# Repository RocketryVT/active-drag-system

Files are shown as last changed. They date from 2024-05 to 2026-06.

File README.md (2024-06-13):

# Active Drag System (ADS)
This is the main codebase for Rocketry at Virginia Tech's Active Drag System, also known colloquially as the ADS, for the 2023-2024 competition year. It runs primarily on a Raspberry Pi Pico, and its goal is to autonomously control the ADS' deployment during flight.

`Eigen` Library, `cmake`, and `arm-none-eabi-gcc` tooling required for successful build.

## Clone

**Note: You must initialize the git submodules prior to utilizing CMake for a proper build.**

```shell
git clone https://github.com/RocketryVT/active-drag-system.git
cd active-drag-system/
git submodule update --init --recursive
```

## Build (Linux)
```shell
cmake -B build
cmake --build build
```
In the event that your preferred IDE has trouble locating header files and/or is displaying incorrect errors, pass ```-DCMAKE_EXPORT_COMPILE_COMMANDS=true``` to the first CMake command above. Similarly, if you wish to compile the additional tools (e.g. reading flash, calibrating the IMU, etc.), pass ```-DCOMPILE_TOOLS=true``` to the first CMake command above as well.

## Build (Windows)
Enable WSL2 in windows
Install Ubuntu 22 LTS from Windows Store
```shell
sudo apt update && upgrade
sudo apt install build-essential cmake gcc-arm-none-eabi
```
Then to actually build:
```shell
cmake -B build
cmake --build build
```

## Build Alternative (Mac)
```shell
brew install arm-none-eabi-gcc
```
To check if installed correctly run:
```shell
ls /opt/homebrew/bin | grep "none"
```
you should see a list including but not limited to:
```shell
arm-none-eabi-gcc
arm-none-eabi-g++
```
Next:
```shell
cmake -B build
cmake --build build
```

Binary files should be located in build/src/*.uf2 after a successful build.

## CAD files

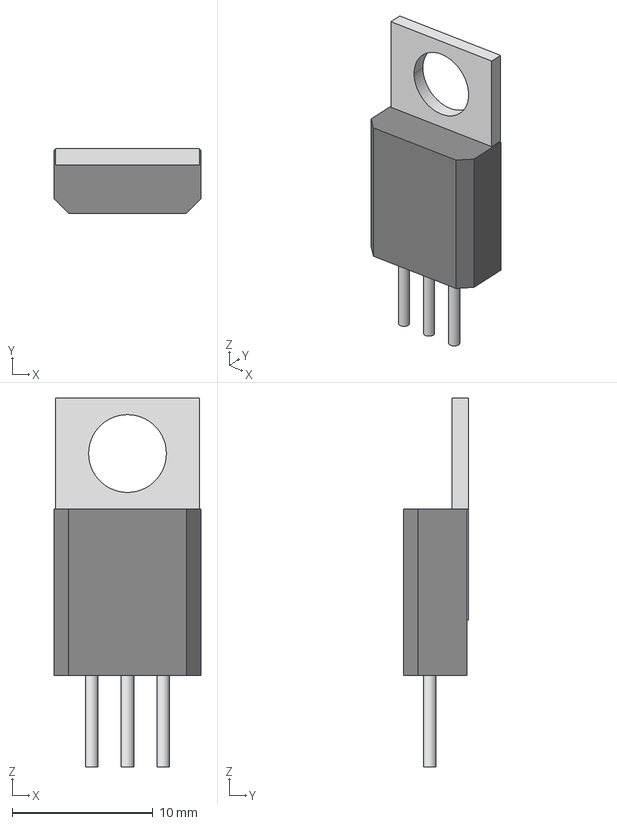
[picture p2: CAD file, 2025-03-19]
hardware/models/STP55NF06.step
10.4 x 4.60 x 26.2 mm

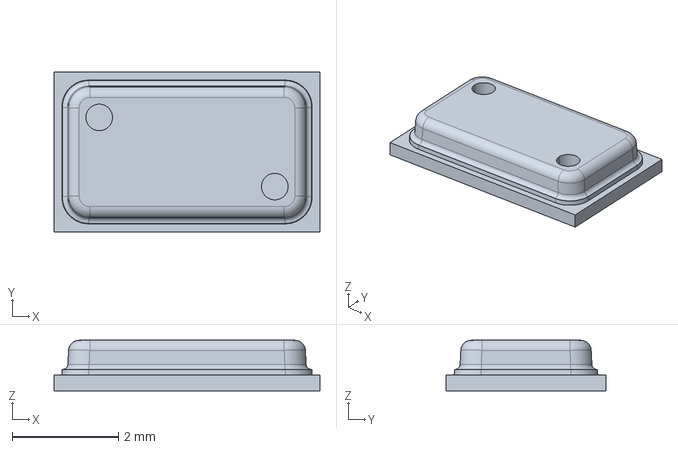
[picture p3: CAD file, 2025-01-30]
hardware/models/c-ms560702ba03-50-a-3d.stp
5.00 x 3.00 x 0.95 mm

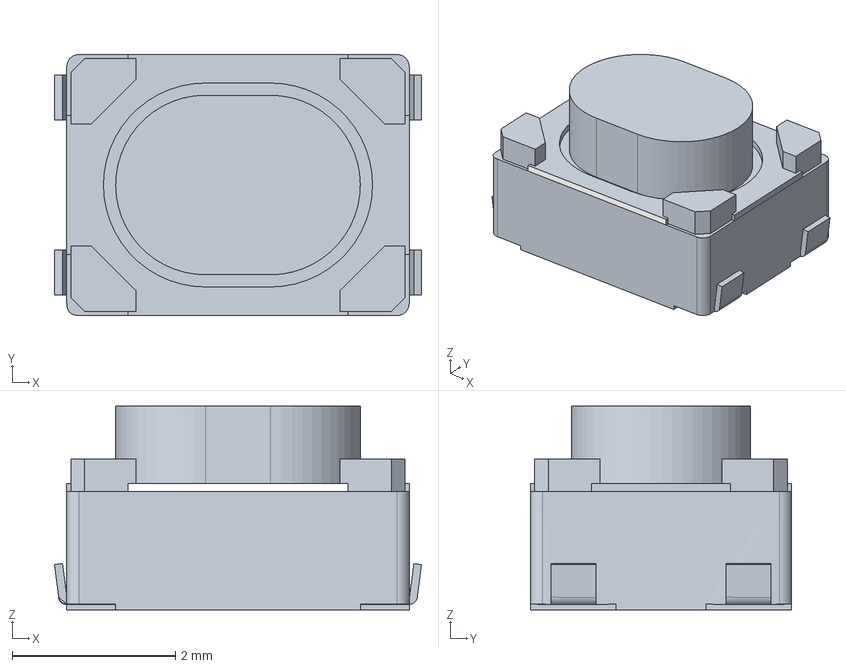
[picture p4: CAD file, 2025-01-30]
hardware/models/PTS815SJG250SMTRLFS.stp
4.50 x 3.20 x 2.50 mm
PTS815SJG250SMTRLFS_PART1
PTS815SJG250SMTRLFS_PART2
PTS815SJG250SMTRLFS_PART3

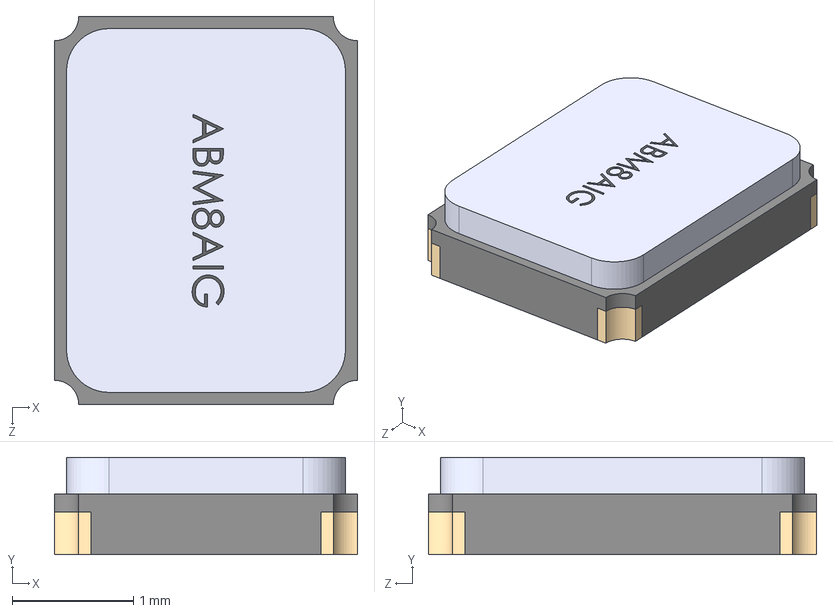
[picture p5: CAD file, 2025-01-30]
hardware/models/ABM8AIG-12.000MHZ-12-2Z-T3.step
2.50 x 0.801 x 3.20 mm

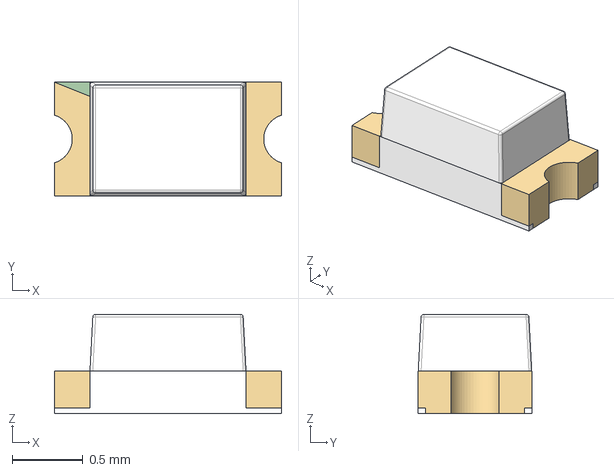
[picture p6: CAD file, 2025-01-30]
hardware/models/WL-SMCW_0603.step
1.60 x 0.8 x 0.7 mm

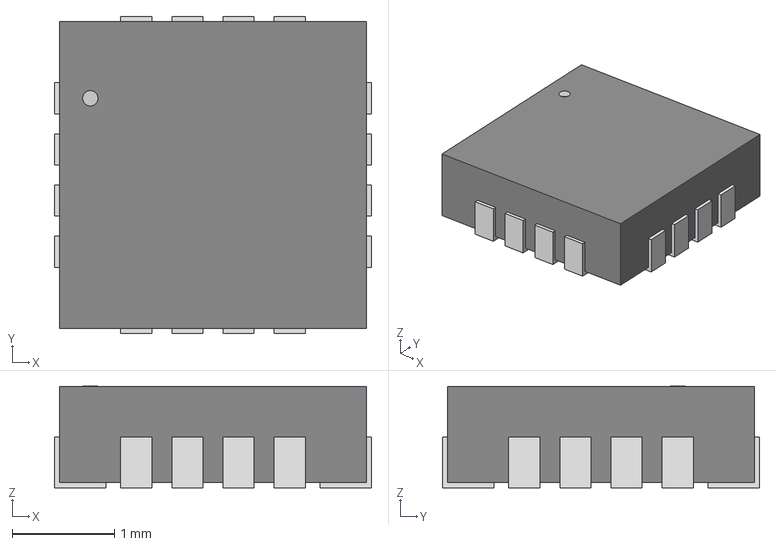
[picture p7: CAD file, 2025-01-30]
hardware/models/MMC5983MA_MEM.step
3.10 x 3.10 x 0.993 mm

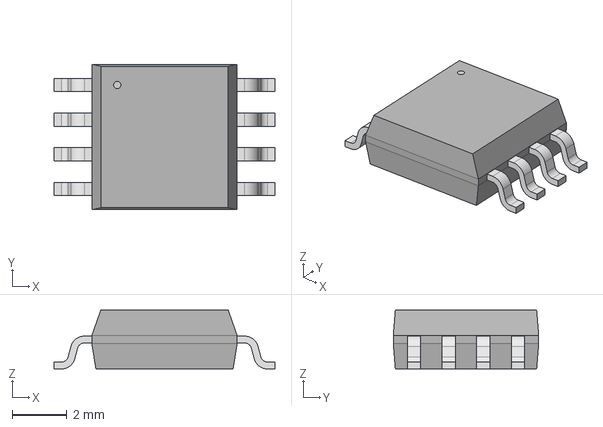
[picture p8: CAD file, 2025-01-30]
hardware/models/SOIC_128JVSIQ_WIN.step
8.10 x 5.33 x 2.16 mm

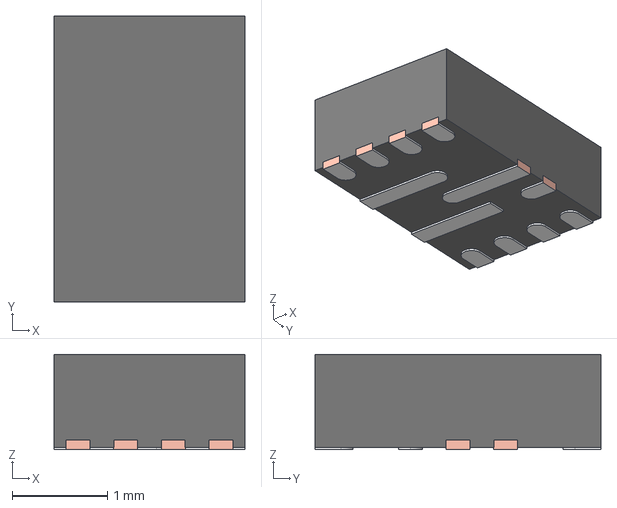
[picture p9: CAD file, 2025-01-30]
hardware/models/RJN0012A.stp
2.00 x 3.00 x 1.00 mm
FRAME
MOLD

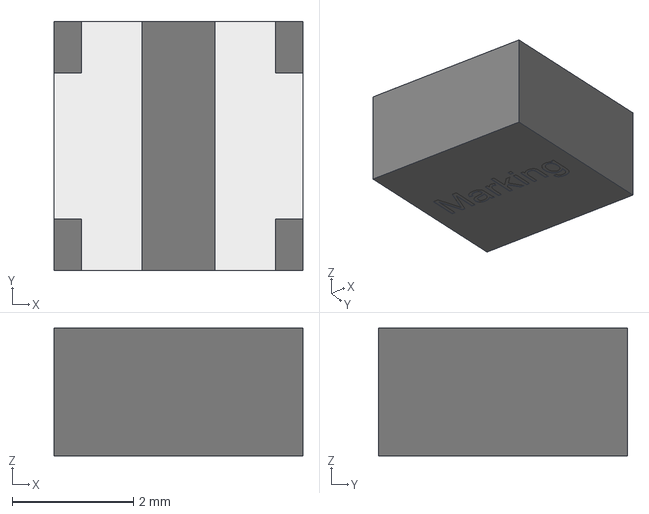
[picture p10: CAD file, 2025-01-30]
hardware/models/WE-MAIA_4020.step
4.10 x 4.10 x 2.10 mm
body_SSMC_403020
land_pattern_SSMC_403020 x 2

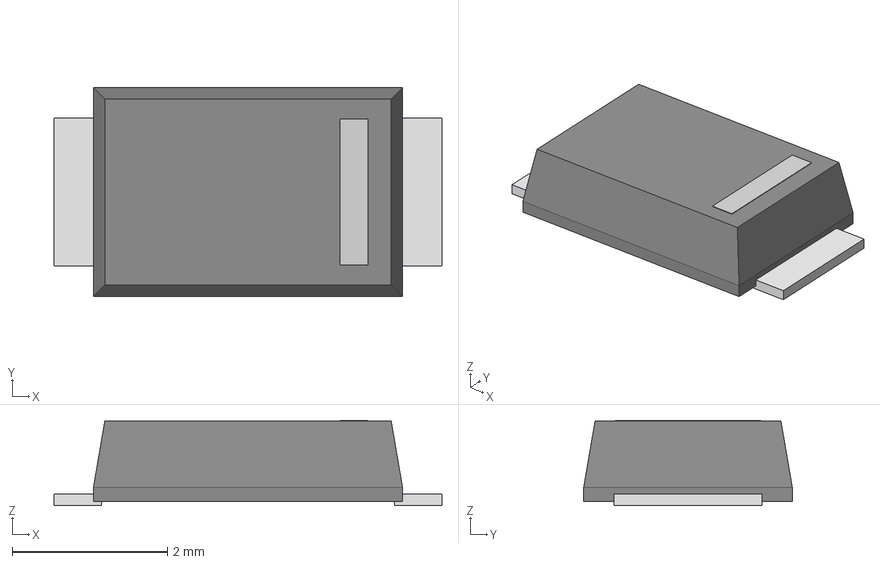
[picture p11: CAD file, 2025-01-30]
hardware/models/SDO_CFP5_SOD128_NEX.step
5.00 x 2.69 x 1.10 mm

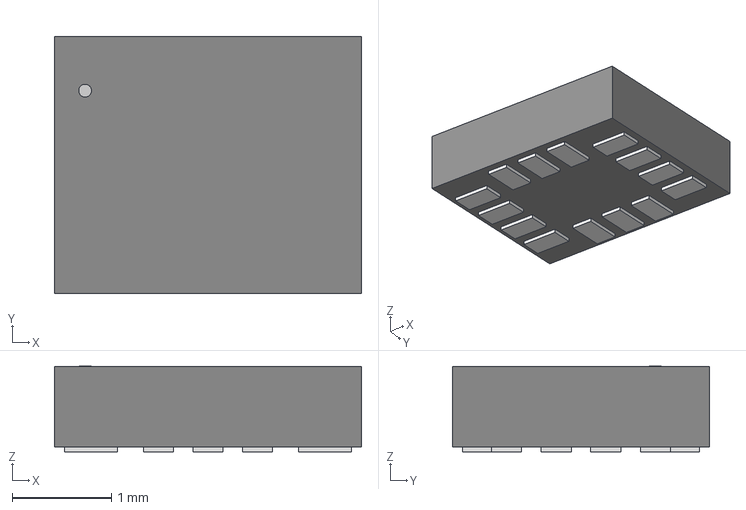
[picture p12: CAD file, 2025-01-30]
hardware/models/LGA14L_LSM6_STM.step
3.10 x 2.59 x 0.866 mm

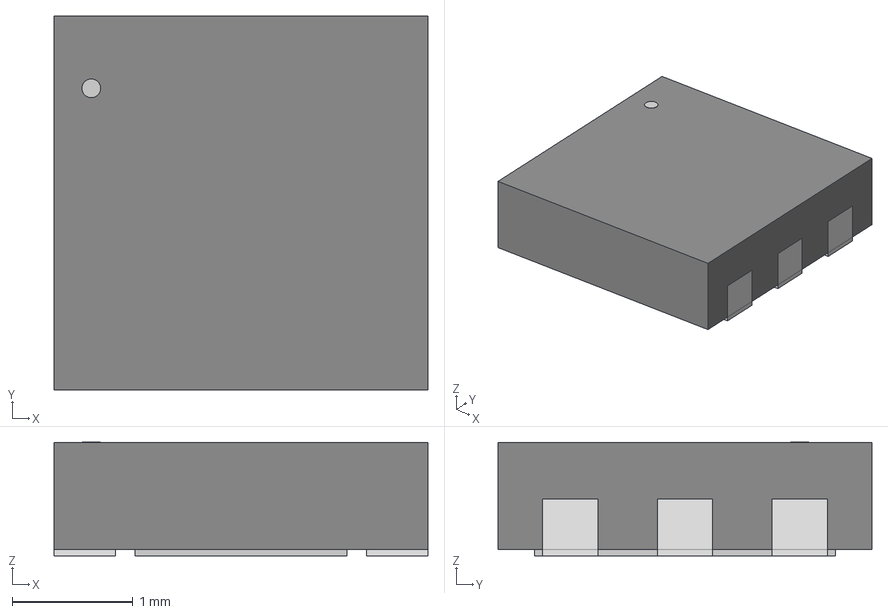
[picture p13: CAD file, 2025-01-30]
hardware/models/SON_DFN6_3X3_STM.step
3.10 x 3.10 x 0.942 mm

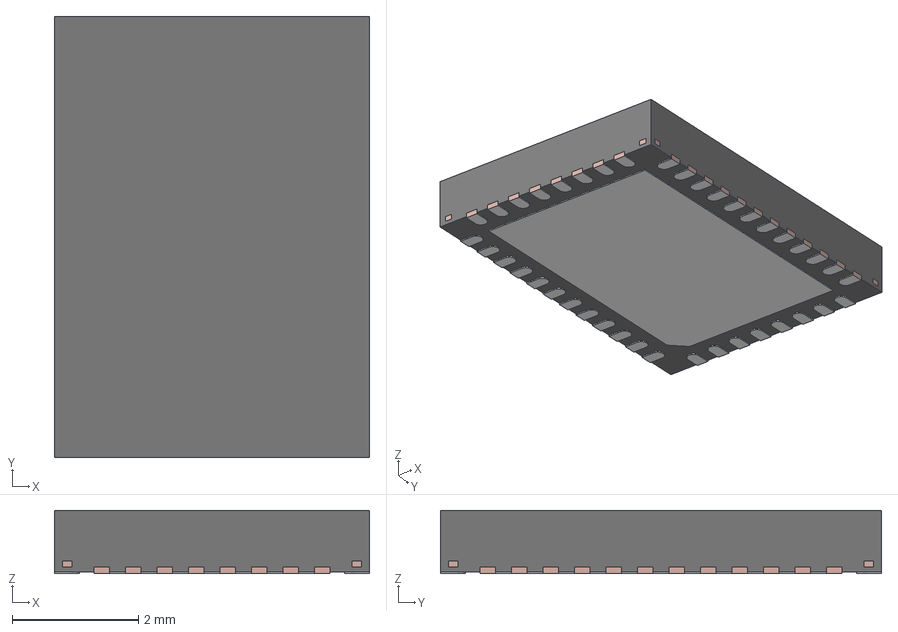
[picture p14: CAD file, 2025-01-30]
hardware/models/RGF0040E.stp
5.00 x 7.00 x 1.00 mm
FRAME

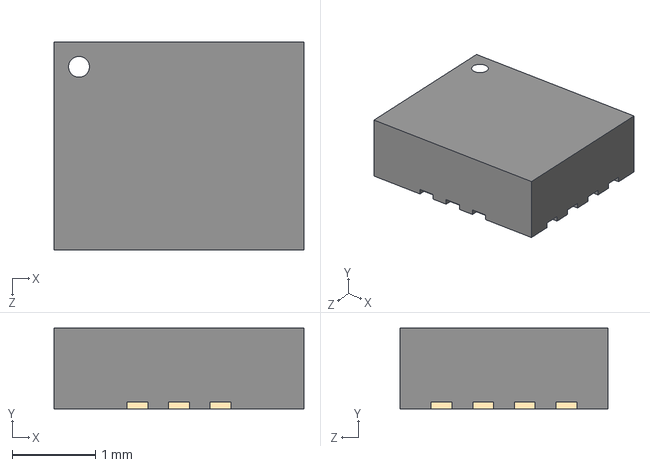
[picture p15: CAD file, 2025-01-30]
hardware/models/IIM-42653.step
3.00 x 0.97 x 2.50 mm

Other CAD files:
hardware/models/LGA_CC-14-1_ADI.step
hardware/models/10118193-0001LF.step

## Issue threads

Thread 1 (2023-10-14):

Sensor Usage Implementation

dawsynth, 2023-10-14:
This is the ongoing issue for the implementation of the communication between the BeagleBone and any sensors (primarily the IMU and Altimeter). This will likely be accomplished via one of the Programmable Real-time Units (PRU) featured on the BeagleBone Black. The PRUs are essentially co-processors that lives on the same board for easing repetitive processes (such as input/output) off of the main CPU. A couple of references for the PRUs' usage can be found in the last chapters of the book "Exploring BeagleBone" by Derek Molloy as well as at [this website](https://www.glennklockwood.com/embedded/beaglebone-pru.html). A current, working design (in pseudo-code) for the class structure is as follows:

```
class Sensor {
    private Logger log;
    private altimeterSetup();
    private imuSetup();
    update();
}
```

Please document any updates or changes made for this implementation within this issue's thread.

gregoryw3, 2023-10-31:
- Using Boost::ASIO for asynchronous non blocking I/O access. Allows simultaneous reading and writing.
    - https://gist.github.com/kaliatech/427d57cb1a8e9a8815894413be337cf9
    - Using this as guide for implementing Boost::ASIO
- Found reference Adafruit cpp files we can use for BNO055 (imu) and MPL3115A2 (alt) as a basis
   - They both rely on arduino libraries so we can't use them directly but they tell us the control flow and memory addresses to use.
- Don't understand how servos work (in c++)?
   - Is it just sending an int to a /dev/ gpio and thats it?
   - https://stackoverflow.com/questions/71042253/what-are-my-options-for-pwm-using-c-on-the-google-coral-dev-board
      - ```shell
        echo 0 > /sys/class/pwm/pwmchip0/export
        echo 50000 > /sys/calss/pwm/pwmchip0/pwm0/period
        echo 25000 > /sys/calss/pwm/pwmchip0/pwm0/duty_cycle
        ehco 1 > /sys/calss/pwm/pwmchip0/pwm0/enable
        ```

dawsynth, 2023-10-31:
So to answer your question on how servos work, I believe it is a matter of just writing the desired values to the correct memory addresses. There is an example in the book on how to control a PWM signal via the PRU in C. It should be on page 704, but here is the provided source straight from the book:

```C
#include <stdint.h>
#include <pru_cfg.h>
#include "resource_table_empty.h"
// Delay factor which defines the PWM frequency
#define DELAYFACTOR 10
volatile register uint32_t __R30;
volatile register uint32_t __R31;

void main(void) {
  volatile uint32_t gpio, button;
  uint32_t percent, count;
  // The PWM percentage (0-100) for the positive cycle
  percent = 75;
  // Use pru0_pru_r30_5 as an output i.e., 100000 or 0x0020
  gpio = 0x0020;
  // Use pru0_pru_r31_3 as a button i.e., 1000 or 0x0008
  button = 0x0008;
  // Stop the loop when the button is pressed
  while (!(__R31 && button)) {
    for(count=0; count<100; count++) {
      // Use two comparisons to equalize the timing
      if(count<=percent) { __R30 |= gpio; }
      if(count> percent) { __R30 &= (~gpio); }
      __delay_cycles(DELAYFACTOR);
    }
  }
  __halt();
}
```

One thing I find interesting in this implementation is its direct use of registers within C. Not something you see everyday, even in embedded devices.

gregoryw3, 2023-10-31:
Thanks! Although both adafruit sensors also use direct registers. So idk if thats for the onboard module firmware or for users...

Closed 2024-05-09.

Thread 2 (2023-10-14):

Active Drag System Class Implementation

dawsynth, 2023-10-14:
This is the ongoing issue for the implementation of the ADS Class. This class will primarily deal with the algorithmic side of the Active Drag System using data provided by the sensors. This will be located on the main CPU and be constantly running updates and status checks while the rocket is in the air. This class will also feature a Kalman Filter for smoothing of the sensor data and a logger for recording significant information. A current, working design (in pseudo-code) for the class structure is as follows:

```
class ADS {
Private:
    KalmanFilter kf;
    Logger log;
    rocketState;

    surfaceModelFit();
    ADSPlan();
    updateRocketState();
    angleFromPercentage();
    readSensor();
    actuatorDeploy(angle);
Public:
    run();
}
```

Please document any updates or changes made for this implementation within this issue's thread

Closed 2024-05-09.

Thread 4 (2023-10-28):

Current status of Kalman Filter & Logger

JazzJackson0, 2023-10-28:
Unfinished code. Using `cmake` to compile these.

**Kalman Filter:** Will likely make `makeInit()` more generic to allow for customizable matrix sizes. I think there is a design pattern that will allow me to make a more generic function without requiring a monstrous constructor to set the matrix sizes (Maybe a Builder Pattern? Not sure yet).
Also, the interactions between the matrix operations probably have errors. I haven't dealt with it yet.
I have a GoogleTest fixture for this but I haven't started writing the test functions yet.
Also, I'm using `Eigen` for the Linear Algebra because why the hell would I use `Boost`.

**KalmanFilter.cpp**
```c++
#include "kalmanfilter.hpp"

// Private----------------------------------------------------------------------
void KalmanFilter::matrixInit() {

    // Probably will make this more generic with some type of Design Pattern

    I = MatrixXf::Identity(2, 2);

    // Setup State Transition Matrix
    F(2, 2);
    F << 1.0, dt,
        0.0, 1.0;

    // Setup Control Input Matrix
    B(2, 1);
    B << 0.5*std::pow(dt, 2), // (Linear Displacement Eq.)
        dt;

    // Setup Measurement Matrix
    H.setIdentity(1, 2);

    // Setup Process-Noise Covariance
    Q.setIdentity(2, 2);

    // Setup Measurement Covariance
}

void KalmanFilter::prediction(VectorXf input_vec) {

    x = (F * x) + (B * input_vec);
    P = (F * (P * F.transpose())) + Q;
}

void KalmanFilter::update(float measurement) {

    // Innovation
    float y = measurement - (H * x)(0, 0);

    // Residual/Innovation Covariance
    MatrixXf S = (H * (P * H.transpose())) + R;

    // Kalman Gain
    MatrixXf K = (P * H.transpose()) * S.inverse();

    // Update
    x = x + (K * y);
    P = (I - (K * H)) * P;
}

// Public----------------------------------------------------------------------
KalmanFilter::KalmanFilter() {

    x.setZero(2);
    P.setZero(2, 2);
    dt = 1;
    matrixInit();

}

KalmanFilter::KalmanFilter(VectorXf state_vec, MatrixXf state_cov, float time_step) {

    x = state_vec;
    P = state_cov;
    dt = time_step;
    matrixInit();
}

void KalmanFilter::run(VectorXf input_vec, float measurement) {

    prediction(input_vec);
    update(measurement);
}
```
**KalmanFilter.hpp**
```c++
#pragma once
#include "eigen3/Eigen/Dense"
#include <iostream>
#include <cmath>

using namespace Eigen;

class KalmanFilter {

    private:

        VectorXf x; // State Vector
        MatrixXf P; // State Covariance

        MatrixXf F; // State Transition Matrix
        MatrixXf B; // Control Input Matrix
        MatrixXf H; // Measurement Matrix

        MatrixXf Q; // Process-Noise Covariance
        MatrixXf R; // Measurement Covariance

        MatrixXf I; // Identity

        float dt;

        /**
         * @brief Initialize all necessary matrices.
         *
         */
        void matrixInit();

        /**
         * @brief Predict current State Vector & State Covariance
         * given the current control input.
         *
         * @param input_vec The control input to be applied to the
         * previous State Vector
         */
        void prediction(VectorXf input_vec);

        /**
         * @brief Correct the State Vector & State Covariance predictions
         * given a related current measurement.
         *
         * @param measurement Current measurement
         */
        void update(float measurement);

    public:

        /**
         * @brief Construct a new Kalman Filter object
         * With zero-initialized State Vector & State Covariance
         * and dt (time step) initialized to 1.
         *
         */
        KalmanFilter();

        /**
         * @brief Construct a new Kalman Filter object
         *
         * @param state_vec Initial State Vector
         * @param state_cov Initial State Covariance
         * @param time_step Filter Update Interval
         */
        KalmanFilter(VectorXf state_vec, MatrixXf state_cov, float time_step);

        /**
         * @brief Perform Kalman Filter operation with given control input vector
         * and measurement.
         *
         * @param input_vec
         * @param measurement
         */
        void run(VectorXf input_vec, float measurement);
};
```

**Logger:** Will be adding the timestamp stuff, and finishing formatting & printLog().

**Logger.cpp**
```c++
#include "logger.hpp"

Logger::Logger(string _filename) {

    filename = _filename;
}

bool Logger::openLog() {

    file.open(filename);
}

bool Logger::closeLog() {

    file.close();
}

bool Logger::writeToLog(string data) {

    // Add timestamp of Log

    string timestamp;

    file << timestamp << data << '\n';
}

bool Logger::logError(string data) {

    file << "ERROR: " << data << '\n';
}

void Logger::printLog() {

}
```

**Logger.hpp**
```c++
#pragma once
#include <iostream>
#include <fstream>
#include <ctime>
#include <string>
using namespace std;

class Logger {

    private:
        ofstream file;
        string filename;
        time_t startTime;

    public:

        Logger(string _filename);

        bool openLog();

        bool closeLog();

        bool writeToLog(string data);

        bool logError(string data);

        void printLog();
};
```

Closed 2024-05-09.

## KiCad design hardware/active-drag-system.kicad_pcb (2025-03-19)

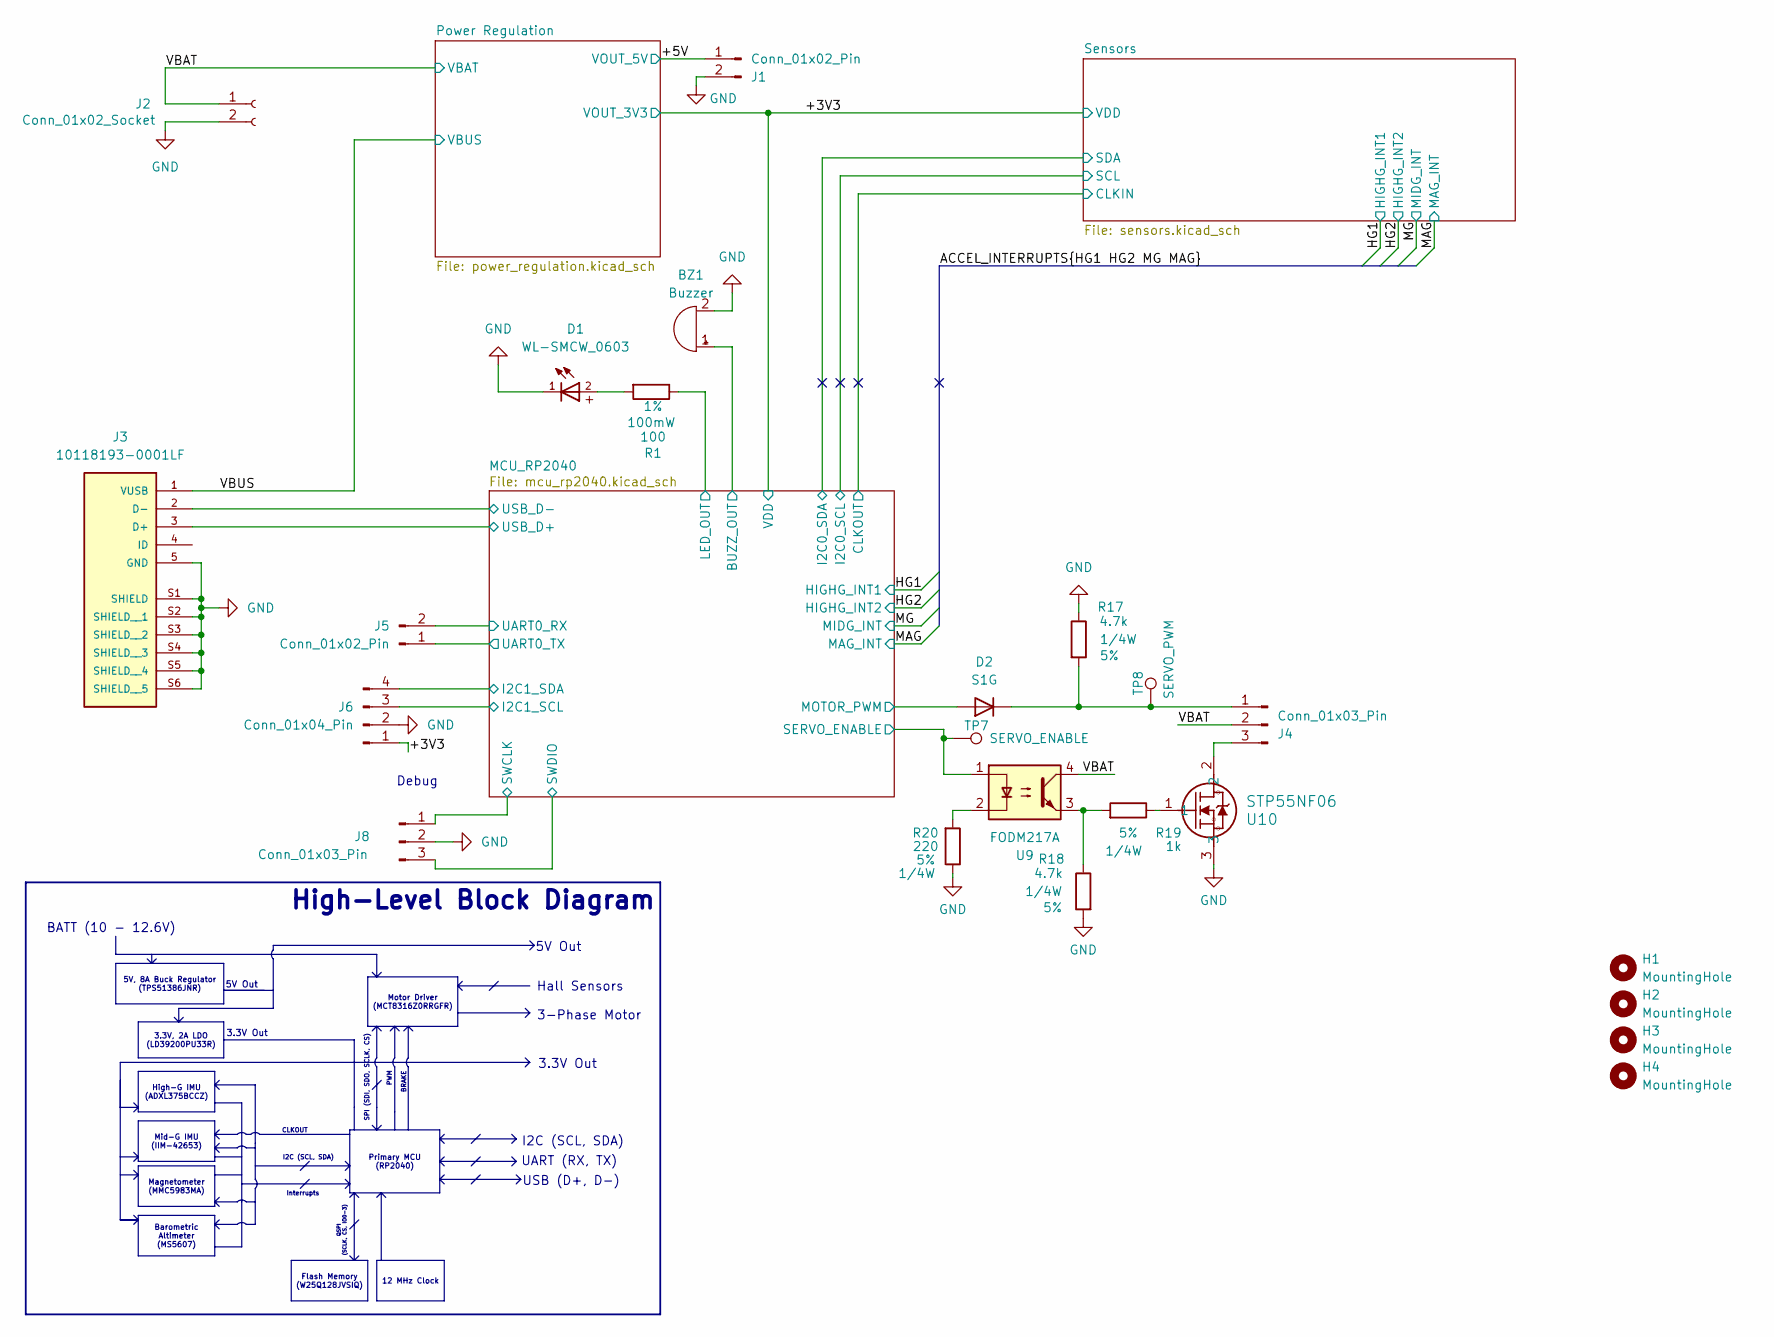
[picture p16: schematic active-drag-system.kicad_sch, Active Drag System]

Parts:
BZ1: Buzzer; Buzzer_12x9.5RM7.6
D1: WL-SMCW_0603; Digikey Part Number 732-4980-1-ND
D2: S1G; D_SMA; Digikey Product Number 1655-S1GCT-ND
H1, H2, H3, H4: MountingHole; MountingHole_2.7mm_M2.5
J1, J5: Conn_01x02_Pin; PinHeader_1x02_P2.54mm_Vertical
J2: Conn_01x02_Socket; SolderWire-2sqmm_1x02_P7.8mm_D2mm_OD3.9mm
J3: 10118193-0001LF; AMPHENOL_10118193-0001LF; PARTREV E; Digikey Part Number 609-4616-1-ND
J4, J8: Conn_01x03_Pin; PinHeader_1x03_P2.54mm_Vertical
J6: Conn_01x04_Pin; PinHeader_1x04_P2.54mm_Vertical
R1: 100; R_0603_1608Metric_Pad0.98x0.95mm_HandSolder; Tolerance 1%; Digikey Part Number P100HCT-ND
R17, R18: 4.7k; R_1206_3216Metric; Tolerance 5%; Digikey Part Number RMCF1206JT4K70CT-ND
R19: 1k; R_1206_3216Metric; Tolerance 5%; Digikey Part Number RMCF1206JT1K00CT-ND
R20: 220; R_1206_3216Metric; Tolerance 5%; Digikey Part Number RMCF1206JT220RCT-ND
TP7: SERVO_ENABLE; TestPoint_Pad_1.0x1.0mm
TP8: SERVO_PWM; TestPoint_Pad_1.0x1.0mm
U9: FODM217A; SOP-4_4.4x2.6mm_P1.27mm
U10: STP55NF06

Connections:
/+3V3: J6.1; also elsewhere on the board
/+5V: J1.1; also elsewhere on the board
/MCU_RP2040/BUZZ_OUT: BZ1.1 (+); also elsewhere on the board
/MCU_RP2040/I2C1_SCL: J6.3; also elsewhere on the board
/MCU_RP2040/I2C1_SDA: J6.4; also elsewhere on the board
/MCU_RP2040/LED_OUT: R1.1; also elsewhere on the board
/MCU_RP2040/MOTOR_PWM: D2.2 (A); also elsewhere on the board
/MCU_RP2040/SERVO_ENABLE: TP7.1, U9.1; also elsewhere on the board
/MCU_RP2040/SWCLK: J8.1; also elsewhere on the board
/MCU_RP2040/SWDIO: J8.3; also elsewhere on the board
/MCU_RP2040/UART0_RX: J5.2; also elsewhere on the board
/MCU_RP2040/UART0_TX: J5.1; also elsewhere on the board
/MCU_RP2040/USB_D+: J3.3 (D+); also elsewhere on the board
/MCU_RP2040/USB_D-: J3.2 (D-); also elsewhere on the board
/VBAT: J2.1, J4.2, U9.4; also elsewhere on the board
/VBUS: J3.1 (VUSB); also elsewhere on the board
GND: BZ1.2 (-), D1.1, J1.2, J2.2, J3.5 (GND), J3.S1 (SHIELD), J3.S2 (SHIELD__1), J3.S3 (SHIELD__2), J3.S4 (SHIELD__3), J3.S5 (SHIELD__4), J3.S6 (SHIELD__5), J6.2, J8.2, R17.1, R18.2, R20.1, U10.3; also elsewhere on the board
unnamed: D1.2, R1.2
unnamed: D2.1 (K), J4.1, R17.2, TP8.1
unnamed: J4.3, U10.2
unnamed: R18.1, R19.2, U9.3
unnamed: R19.1, U10.1
unnamed: R20.2, U9.2

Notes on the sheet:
PWM
Debug
5V Out
CLKOUT
Interrupts
3.3V Out
QSPI (SCLK, CS, IO0-3)
USB (D+, D-)
I2C (SCL, SDA)
3-Phase Motor
BRAKE
High-Level Block Diagram
BATT (10 - 12.6V)
UART (RX, TX)
Hall Sensors
SPI (SDI, SDO, SCLK, CS)
Primary MCU (RP2040)
Flash Memory (W25Q128JVSIQ)
Barometric Altimeter (MS5607)
High-G IMU (ADXL375BCCZ)
12 MHz Clock
3.3V, 2A LDO (LD39200PU33R)
5V, 8A Buck Regulator (TPS51386JNR)
Mid-G IMU (IIM-42653)
Motor Driver (MCT8316Z0RRGFR)
Magnetometer (MMC5983MA)

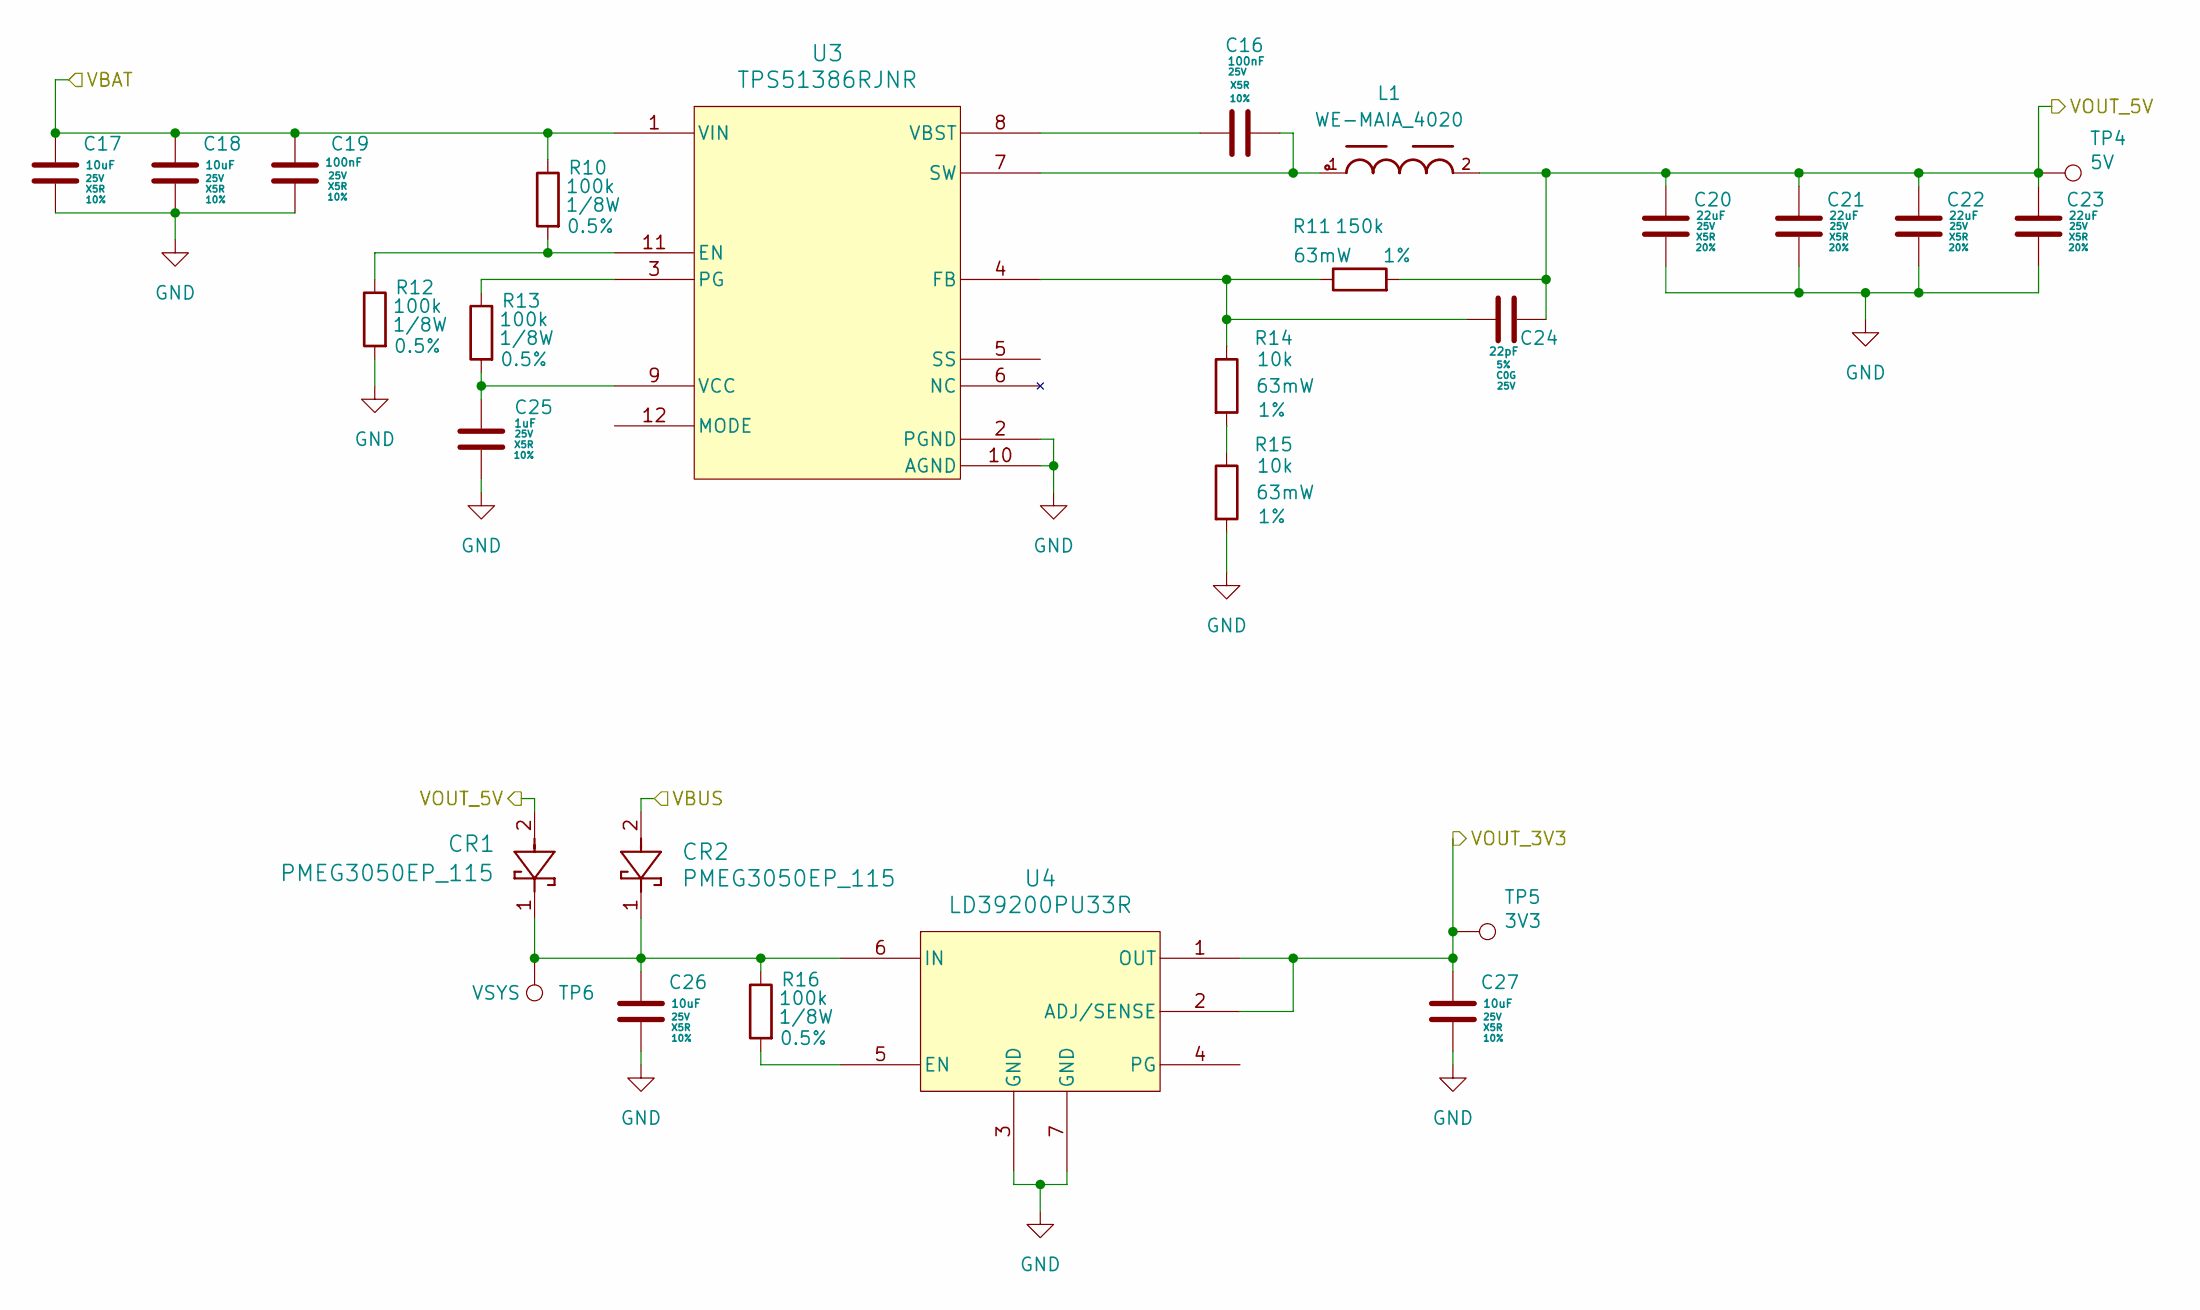
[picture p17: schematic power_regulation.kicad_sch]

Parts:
C16, C19: 100nF; C_0603_1608Metric; Max Voltage 25V; Tolerance 10%; Digikey Part Number 1276-1857-1-ND
C17, C18, C26, C27: 10uF; C_0805_2012Metric; Max Voltage 25V; Tolerance 10%; Digikey Part Number 490-10748-1-ND
C20, C21, C22, C23: 22uF; C_0805_2012Metric; Max Voltage 25V; Tolerance 20%; Digikey Part Number 1276-7092-1-ND
C24: 22pF; C_0603_1608Metric; Max Voltage 25V; Tolerance 5%; Digikey Part Number 1292-1503-1-ND
C25: 1uF; C_0805_2012Metric; Max Voltage 25V; Tolerance 10%; Digikey Part Number 311-1868-1-ND
CR1, CR2: PMEG3050EP_115; SDO_CFP5_SOD128_NEX; Digikey Part Number 1727-5317-1-ND
L1: WE-MAIA_4020; Digikey Part Number 732-11312-1-ND
R10, R12, R13, R16: 100k; R_0805_2012Metric; Tolerance 0.5%; Digikey Part Number P123795CT-ND
R11: 150k; R_0603_1608Metric; Tolerance 1%; LCSC C25755
R14, R15: 10k; R_0603_1608Metric; Tolerance 1%; Digikey Part Number A102203CT-ND
TP4: 5V; TestPoint_Pad_1.0x1.0mm
TP5: 3V3; TestPoint_Pad_1.0x1.0mm
TP6: VSYS; TestPoint_Pad_1.0x1.0mm
U3: TPS51386RJNR; VQFN-HR12_RJN_TEX; Digikey Part Number 296-TPS51386RJNRCT-ND
U4: LD39200PU33R; SON_DFN6_3X3_STM; Digikey Part Number 497-15229-1-ND

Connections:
/+3V3: C27.1, TP5.1, U4.1 (OUT), U4.2 (ADJ/SENSE); also elsewhere on the board
/+5V: C20.1, C21.1, C22.1, C23.1, C24.2, CR1.2, L1.2, R11.2, TP4.1; also elsewhere on the board
/VBAT: C17.1, C18.1, C19.1, R10.1, U3.1 (VIN); also elsewhere on the board
/VBUS: CR2.2; also elsewhere on the board
GND: C17.2, C18.2, C19.2, C20.2, C21.2, C22.2, C23.2, C25.2, C26.2, C27.2, R12.2, R15.2, U3.2 (PGND), U3.10 (AGND), U4.3 (GND), U4.7 (GND); also elsewhere on the board
unnamed: R14.2, R15.1
unnamed: R10.2, R12.1, U3.11 (EN)
unnamed: C24.1, R11.1, R14.1, U3.4 (FB)
unnamed: R13.1, U3.3 (PG)
unnamed: C16.2, L1.1, U3.7 (SW)
unnamed: C16.1, U3.8 (VBST)
unnamed: C25.1, R13.2, U3.9 (VCC)
unnamed: R16.2, U4.5 (EN)
unnamed: C26.1, CR1.1, CR2.1, R16.1, TP6.1, U4.6 (IN)

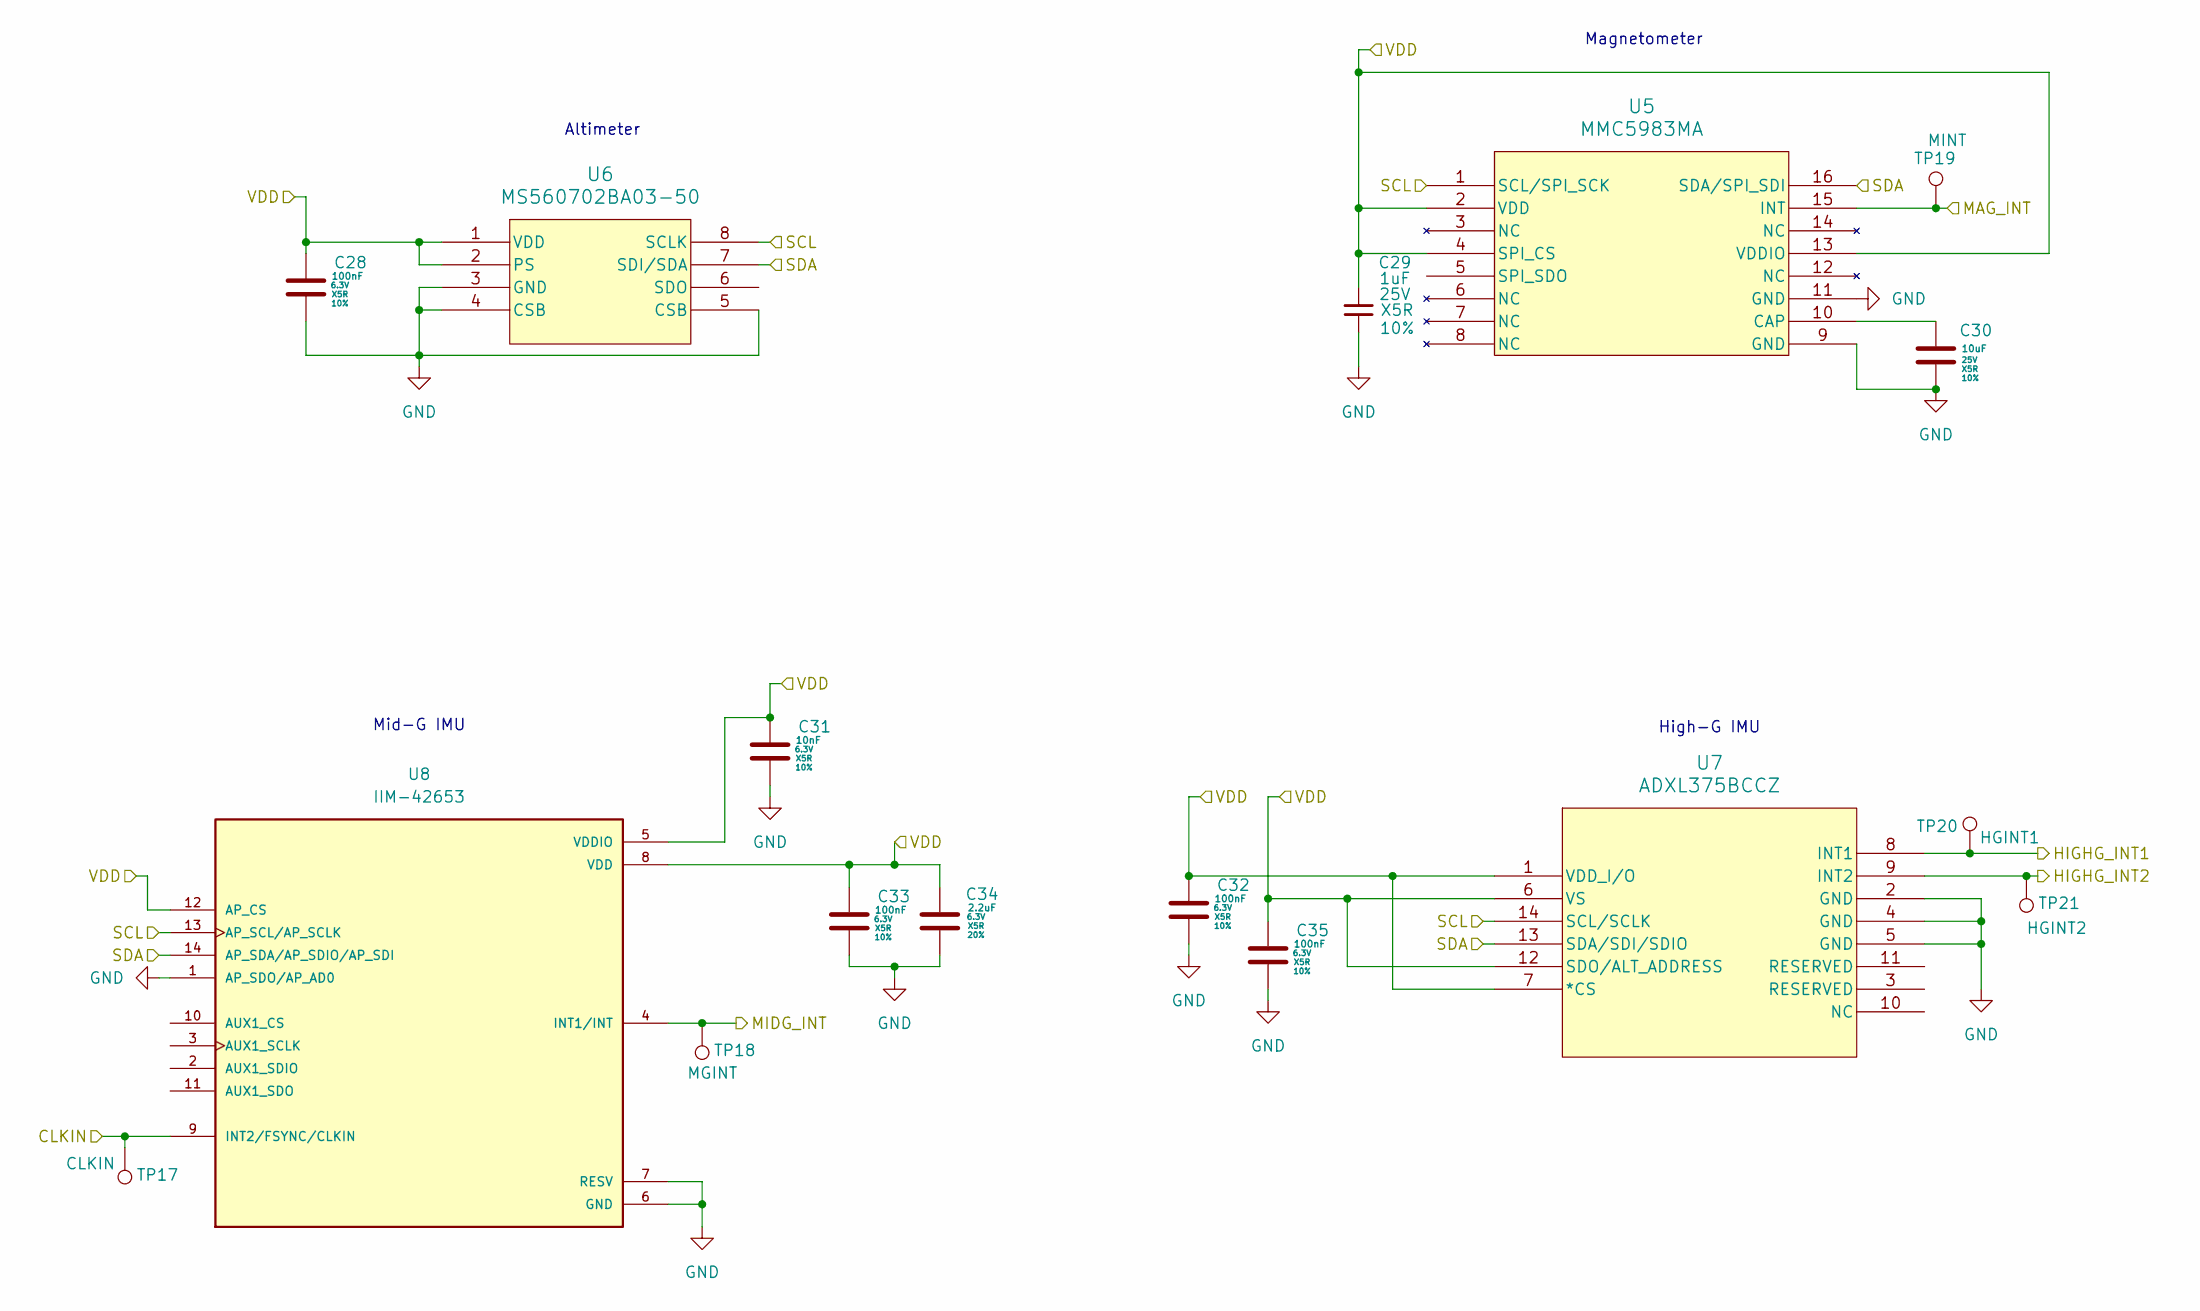
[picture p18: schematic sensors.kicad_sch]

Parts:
C28, C32, C33, C35: 100nF; C_0603_1608Metric; Max Voltage 6.3V; Tolerance 10%; Digikey Part Number 1276-1857-1-ND
C29: 1uF; C_0805_2012Metric; Max Voltage 25V; Tolerance 10%; Digikey Part Number 311-1868-1-ND
C30: 10uF; C_0805_2012Metric; Max Voltage 25V; Tolerance 10%; Digikey Part Number 490-10748-1-ND
C31: 10nF; C_0603_1608Metric; Max Voltage 6.3V; Tolerance 10%; Digikey Part Number 478-KGM15AR51E103KTCT-ND
C34: 2.2uF; C_0805_2012Metric; Max Voltage 6.3V; Tolerance 20%; Digikey Part Number 1276-2955-1-ND
TP17: CLKIN; TestPoint_Pad_1.0x1.0mm
TP18: MGINT; TestPoint_Pad_1.0x1.0mm
TP19: MINT; TestPoint_Pad_1.0x1.0mm
TP20: HGINT1; TestPoint_Pad_1.0x1.0mm
TP21: HGINT2; TestPoint_Pad_1.0x1.0mm
U5: MMC5983MA; MMC5983MA_MEM
U6: MS560702BA03-50; SON8_MS5611_TEC; Digikey Part Number 223-1198-1-ND
U7: ADXL375BCCZ; LGA_CC-14-1_ADI; Digikey Part Number 505-ADXL375BCCZ-ND
U8: IIM-42653; PQFN50P250X300X97-14N; PARTREV 1.1; Digikey Part Number 1428-IIM-42653CT-ND

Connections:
/+3V3: C28.1, C29.2, C31.1, C32.1, C33.1, C34.1, C35.1, U5.2 (VDD), U5.4 (SPI_CS), U5.13 (VDDIO), U6.1 (VDD), U6.2 (PS), U7.1 (VDD_I/O), U7.6 (VS), U7.7 (*CS), U7.12 (SDO/ALT_ADDRESS), U8.5 (VDDIO), U8.8 (VDD), U8.12 (AP_CS); also elsewhere on the board
/HG1: TP20.1, U7.8 (INT1); also elsewhere on the board
/HG2: TP21.1, U7.9 (INT2); also elsewhere on the board
/MAG: TP19.1, U5.15 (INT); also elsewhere on the board
/MCU_RP2040/CLKOUT: TP17.1, U8.9 (INT2/FSYNC/CLKIN); also elsewhere on the board
/MCU_RP2040/I2C0_SCL: U5.1 (SCL/SPI_SCK), U6.8 (SCLK), U7.14 (SCL/SCLK), U8.13 (AP_SCL/AP_SCLK); also elsewhere on the board
/MCU_RP2040/I2C0_SDA: U5.16 (SDA/SPI_SDI), U6.7 (SDI/SDA), U7.13 (SDA/SDI/SDIO), U8.14 (AP_SDA/AP_SDIO/AP_SDI); also elsewhere on the board
/MG: TP18.1, U8.4 (INT1/INT); also elsewhere on the board
GND: C28.2, C29.1, C30.2, C31.2, C32.2, C33.2, C34.2, C35.2, U5.9 (GND), U5.11 (GND), U6.3 (GND), U6.4 (CSB), U6.5 (CSB), U7.2 (GND), U7.4 (GND), U7.5 (GND), U8.1 (AP_SDO/AP_AD0), U8.6 (GND), U8.7 (RESV); also elsewhere on the board
unnamed: C30.1, U5.10 (CAP)

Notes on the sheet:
Magnetometer
Mid-G IMU
High-G IMU
Altimeter

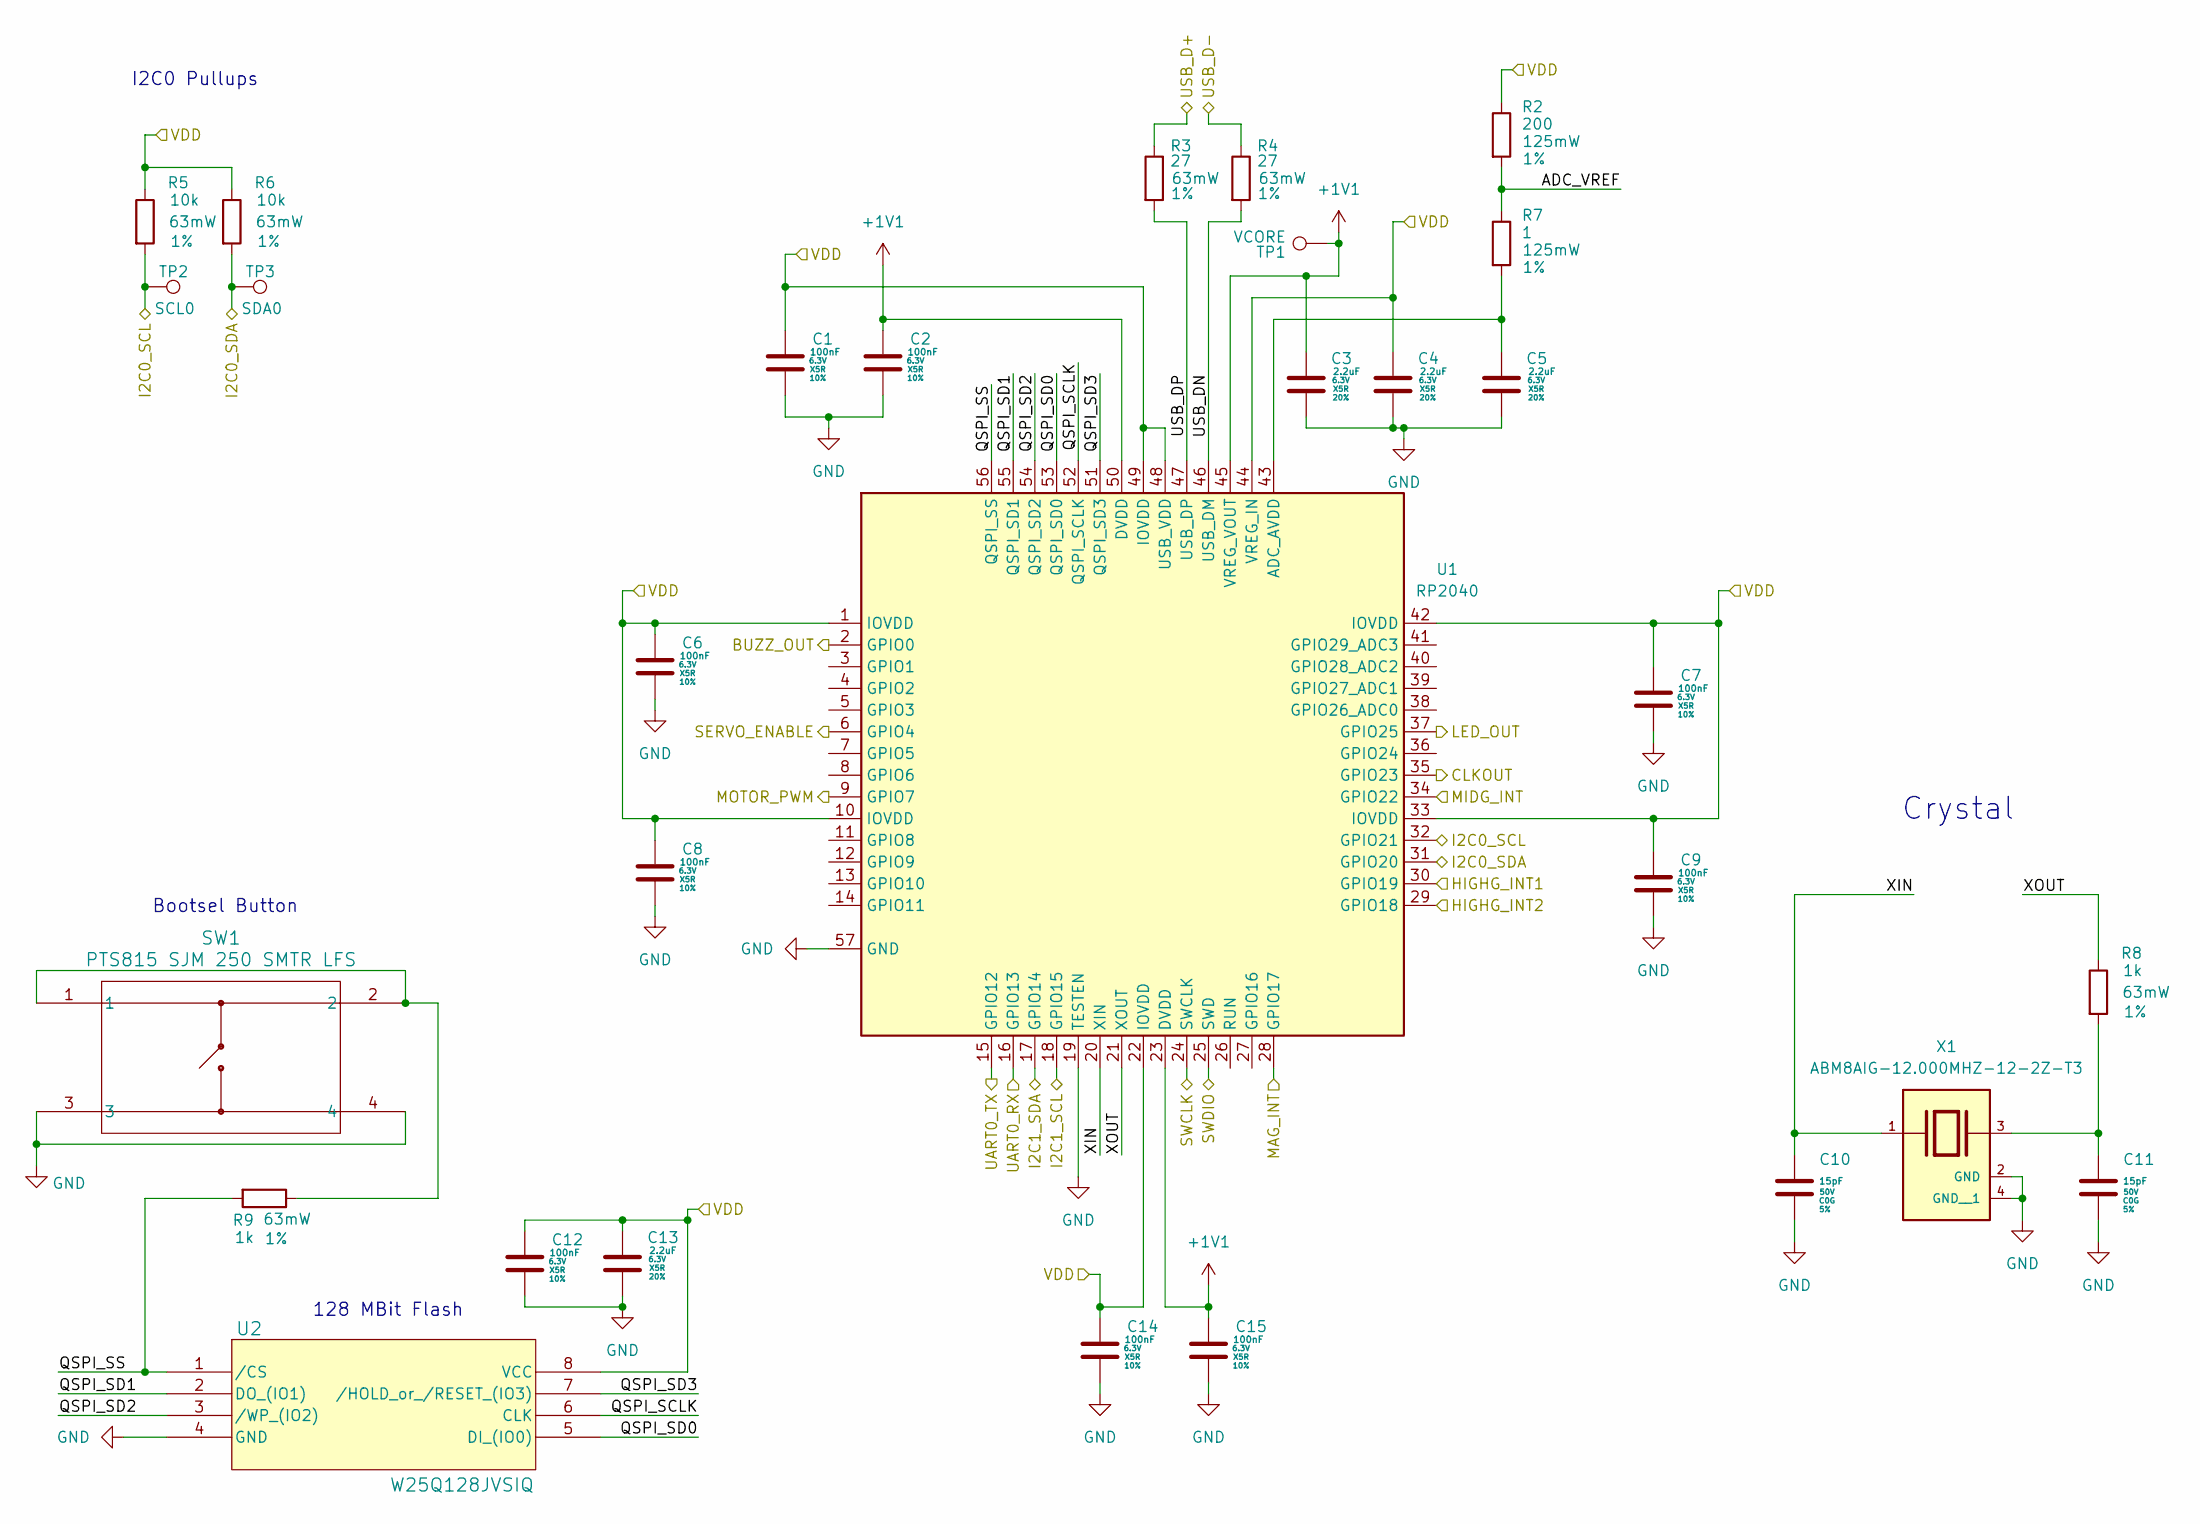
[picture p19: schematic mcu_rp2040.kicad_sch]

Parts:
C1, C2, C6, C7, C8, C9, C12, C14, C15: 100nF; C_0603_1608Metric; Max Voltage 6.3V; Tolerance 10%; Digikey Part Number 1276-1857-1-ND
C3, C4, C5, C13: 2.2uF; C_0805_2012Metric; Max Voltage 6.3V; Tolerance 20%; Digikey Part Number 1276-2955-1-ND
C10, C11: 15pF; C_0603_1608Metric; Max Voltage 50V; Tolerance 5%; Digikey Part Number 1276-1296-1-ND
R2: 200; R_0805_2012Metric; Tolerance 1%; Digikey Part Number P200CCT-ND
R3, R4: 27; R_0603_1608Metric; Tolerance 1%; Digikey Part Number P27.0HCT-ND
R5, R6: 10k; R_0603_1608Metric; Tolerance 1%; Digikey Part Number A102203CT-ND
R7: 1; R_0805_2012Metric; Tolerance 1%; Digikey Part Number P1.0DCT-ND
R8, R9: 1k; R_0603_1608Metric; Tolerance 1%; Digikey Part Number A102226CT-ND
SW1: PTS815 SJM 250 SMTR LFS; SW4_PTS815_SJM_250_SMTR_LFS_CNK; Digikey Part Number CKN12215-1-ND
TP1: VCORE; TestPoint_Pad_1.0x1.0mm
TP2: SCL0; TestPoint_Pad_1.0x1.0mm
TP3: SDA0; TestPoint_Pad_1.0x1.0mm
U1: RP2040; QFN-56-1EP_7x7mm_P0.4mm_EP3.2x3.2mm_ThermalVias; Digikey Part Number 2648-SC0914(13)CT-ND
U2: W25Q128JVSIQ; SOIC_128JVSIQ_WIN; Digikey Part Number W25Q128JVSIQ-ND
X1: ABM8AIG-12.000MHZ-12-2Z-T3; XTAL_ABM8AIG-12.000MHZ-12-2Z-T3; PARTREV 43629; Digikey Part Number 535-13381-1-ND

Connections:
+1V1: C2.1, C3.1, C15.1, TP1.1, U1.23 (DVDD), U1.45 (VREG_VOUT), U1.50 (DVDD)
/+3V3: C1.1, C4.1, C6.1, C7.1, C8.1, C9.1, C12.1, C13.1, C14.1, R2.1, R5.1, R6.1, U1.1 (IOVDD), U1.10 (IOVDD), U1.22 (IOVDD), U1.33 (IOVDD), U1.42 (IOVDD), U1.44 (VREG_IN), U1.48 (USB_VDD), U1.49 (IOVDD), U2.8 (VCC); also elsewhere on the board
/HG1: U1.30 (GPIO19); also elsewhere on the board
/HG2: U1.29 (GPIO18); also elsewhere on the board
/MAG: U1.28 (GPIO17); also elsewhere on the board
/MCU_RP2040/ADC_VREF: R2.2, R7.1
/MCU_RP2040/BUZZ_OUT: U1.2 (GPIO0); also elsewhere on the board
/MCU_RP2040/CLKOUT: U1.35 (GPIO23); also elsewhere on the board
/MCU_RP2040/I2C0_SCL: R5.2, TP2.1, U1.32 (GPIO21); also elsewhere on the board
/MCU_RP2040/I2C0_SDA: R6.2, TP3.1, U1.31 (GPIO20); also elsewhere on the board
/MCU_RP2040/I2C1_SCL: U1.18 (GPIO15); also elsewhere on the board
/MCU_RP2040/I2C1_SDA: U1.17 (GPIO14); also elsewhere on the board
/MCU_RP2040/LED_OUT: U1.37 (GPIO25); also elsewhere on the board
/MCU_RP2040/MOTOR_PWM: U1.9 (GPIO7); also elsewhere on the board
/MCU_RP2040/QSPI_SCLK: U1.52 (QSPI_SCLK), U2.6 (CLK)
/MCU_RP2040/QSPI_SD0: U1.53 (QSPI_SD0), U2.5 (DI_(IO0))
/MCU_RP2040/QSPI_SD1: U1.55 (QSPI_SD1), U2.2 (DO_(IO1))
/MCU_RP2040/QSPI_SD2: U1.54 (QSPI_SD2), U2.3 (/WP_(IO2))
/MCU_RP2040/QSPI_SD3: U1.51 (QSPI_SD3), U2.7 (/HOLD_or_/RESET_(IO3))
/MCU_RP2040/QSPI_SS: R9.2, U1.56 (QSPI_SS), U2.1 (/CS)
/MCU_RP2040/SERVO_ENABLE: U1.6 (GPIO4); also elsewhere on the board
/MCU_RP2040/SWCLK: U1.24 (SWCLK); also elsewhere on the board
/MCU_RP2040/SWDIO: U1.25 (SWD); also elsewhere on the board
/MCU_RP2040/UART0_RX: U1.16 (GPIO13); also elsewhere on the board
/MCU_RP2040/UART0_TX: U1.15 (GPIO12); also elsewhere on the board
/MCU_RP2040/USB_D+: R3.1; also elsewhere on the board
/MCU_RP2040/USB_D-: R4.1; also elsewhere on the board
/MCU_RP2040/USB_DN: R4.2, U1.46 (USB_DM)
/MCU_RP2040/USB_DP: R3.2, U1.47 (USB_DP)
/MCU_RP2040/XIN: C10.1, U1.20 (XIN), X1.1
/MCU_RP2040/XOUT: R8.1, U1.21 (XOUT)
/MG: U1.34 (GPIO22); also elsewhere on the board
GND: C1.2, C2.2, C3.2, C4.2, C5.2, C6.2, C7.2, C8.2, C9.2, C10.2, C11.2, C12.2, C13.2, C14.2, C15.2, SW1.3, SW1.4, U1.19 (TESTEN), U1.57 (GND), U2.4 (GND), X1.2 (GND), X1.4 (GND__1); also elsewhere on the board
unnamed: C11.1, R8.2, X1.3
unnamed: R9.1, SW1.1, SW1.2
unnamed: C5.1, R7.2, U1.43 (ADC_AVDD)

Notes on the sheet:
Bootsel Button
128 MBit Flash
I2C0 Pullups
Crystal

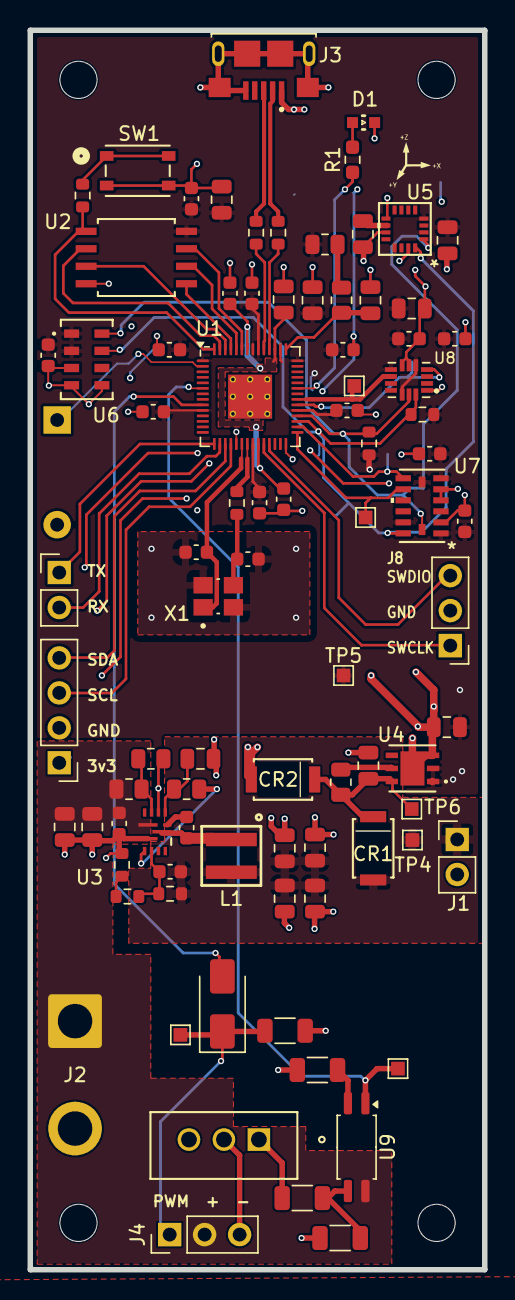
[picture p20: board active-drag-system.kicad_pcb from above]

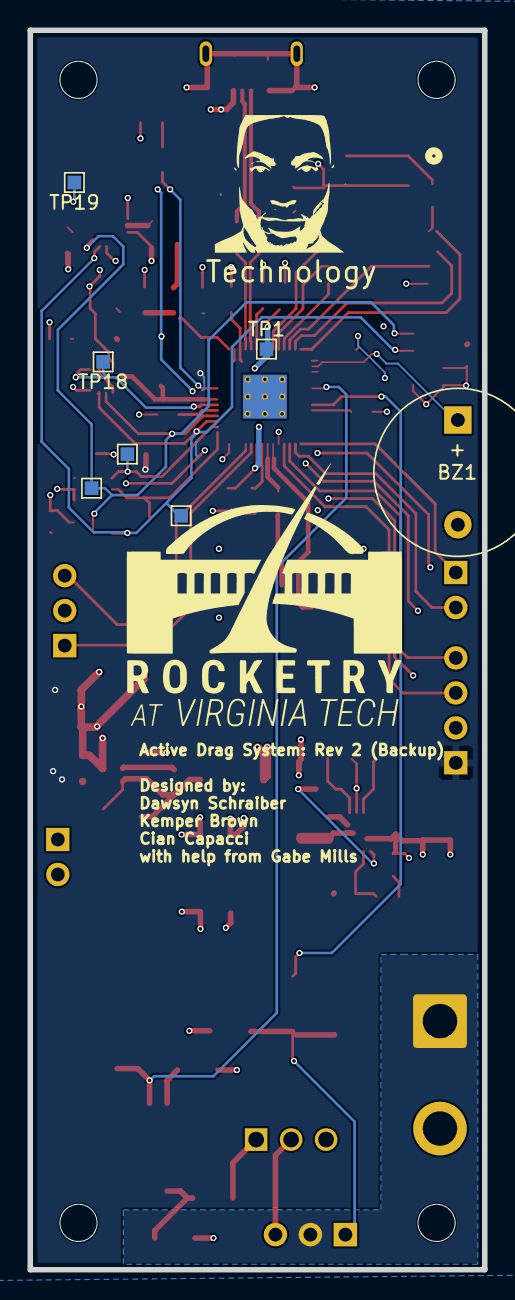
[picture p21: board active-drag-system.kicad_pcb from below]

Board: 4 copper layers, 33.0 x 90.0 mm, 97 parts (7 on the bottom side), 55 nets.

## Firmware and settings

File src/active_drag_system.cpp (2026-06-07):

#include <cstdlib>
#include <pico.h>
#include <stdlib.h>
#include <stdio.h>
#include <string.h>

//<sys/types.h> must be included before <inttypes.h> to fix WSL cmake compilation
#include <sys/types.h>
#include <inttypes.h>

#include "hardware/gpio.h"
#include "hardware/i2c.h"
#include "hardware/adc.h"
#include <hardware/timer.h>
#include "pico/rand.h"
#include "pico/stdlib.h"
#include "pico/stdio.h"
#include "pico/multicore.h"
#include "pico/time.h"
#include <pico/error.h>
#include <pico/types.h>
#include "math.h"

#include "FreeRTOS.h"
#include "FreeRTOSConfig.h"
#include "portmacro.h"
#include "projdefs.h"
#include "serial.hpp"
#include "task.h"
#include "semphr.h"


#include "adxl375.hpp"
#include "ms5607.hpp"
#include "iim42653.hpp"
#include "mmc5983ma.hpp"
#include "pwm.hpp"
#include "pico_logger.hpp"
#include "log_format.hpp"
#include "serial.hpp"
#include "heartbeat.hpp"

#include "kalman_filter.hpp"

/****************************** FREERTOS **************************************/
#define SENSOR_EVENT_HANDLER_PRIORITY   ( tskIDLE_PRIORITY + 7 )
#define SENSOR_SAMPLE_PRIORITY          ( tskIDLE_PRIORITY + 6 )
#define KALMAN_TASK_PRIORITY            ( tskIDLE_PRIORITY + 6 )
#define ROCKET_TASK_PRIORITY            ( tskIDLE_PRIORITY + 4 )
#define ROCKET_EVENT_HANDLER_PRIORITY   ( tskIDLE_PRIORITY + 3 )
#define	HEARTBEAT_TASK_PRIORITY		    ( tskIDLE_PRIORITY + 2 )
#define LOGGING_PRIORITY                ( tskIDLE_PRIORITY + 2 )
#define	SERIAL_TASK_PRIORITY		    ( tskIDLE_PRIORITY + 1 )

void vApplicationTickHook(void) { /* optional */ }
void vApplicationMallocFailedHook(void) { /* optional */ }
void vApplicationStackOverflowHook(TaskHandle_t xTask, char *pcTaskName) { for( ;; ); }

static void logging_task(void* pvParameters);

#define ROCKET_TASK_RATE_HZ 50
volatile TaskHandle_t rocket_task_handle = NULL;
static void rocket_task(void* pvParameters);

#define KALMAN_TASK_RATE_HZ 50
volatile TaskHandle_t kalman_task_handle = NULL;
static void kalman_task(void* pvParameters);

int64_t launch_event_callback(alarm_id_t id, void* user_data);
int64_t coast_event_callback(alarm_id_t id, void* user_data);
int64_t end_event_callback(alarm_id_t id, void* user_data);

volatile TaskHandle_t launch_event_handler_task_handle = NULL;
volatile TaskHandle_t coast_event_handler_task_handle = NULL;
volatile TaskHandle_t end_event_handler_task_handle = NULL;
static void launch_event_handler_task(void* pvParameters);
static void coast_event_handler_task(void* pvParameters);
static void end_event_handler_task(void* pvParameters);

/****************************** FREERTOS **************************************/

/****************************** SERIAL CONSOLE ********************************/
static void read_cmd_func();
static void write_cmd_func();
static void erase_cmd_func();
static void show_cmd_func();
static void deploy_cmd_func();
static void kalman_cmd_func();

const char* executeable_name = "active-drag-system.uf2";
const size_t num_user_cmds = 6;
const command_t user_commands[] = { {.name = "read",
                                     .len = 4,
                                     .function = &read_cmd_func},
                                    {.name = "write",
                                     .len = 5,
                                     .function = &write_cmd_func},
                                    {.name = "erase",
                                     .len = 5,
                                     .function = &erase_cmd_func},
                                    {.name = "show",
                                     .len = 4,
                                     .function = &show_cmd_func},
                                    {.name = "deploy",
                                     .len = 6,
                                     .function = &deploy_cmd_func},
                                    {.name = "kalman",
                                     .len = 6,
                                     .function = &kalman_cmd_func} };
/****************************** SERIAL CONSOLE ********************************/

/****************************** LOGGING ***************************************/
volatile bool use_circular_buffer = true;
volatile TaskHandle_t logging_handle = NULL;
volatile log_entry_t log_entry;

Logger logger(PACKET_SIZE, LOG_BASE_ADDR, print_log_entry);

static void populate_log_entry(log_entry_t* log_entry);
/****************************** LOGGING ***************************************/

volatile bool serial_data_output = false;

MS5607 alt(i2c_default);
ADXL375 adxl375(i2c_default);
IIM42653 iim42653(i2c_default);
MMC5983MA mmc5983ma(i2c_default);

PWM pwm;

#define MOTOR_BURN_TIME 6200
volatile state_t rocket_state = PAD;
volatile uint8_t deployment_percent = 0;

volatile int32_t ground_altitude = 0;
volatile int32_t threshold_altitude = 30;

volatile fix16_t altitude_filt = 0;
volatile fix16_t velocity_filt = 0;

volatile fix16_t drag_force = 0;
volatile fix16_t apogee_prediction = 0;
volatile fix16_t desired_drag_force = 0;
volatile fix16_t desired_deployment = 0;

int main() {
    stdio_init_all();

    adc_init();
    adc_set_temp_sensor_enabled(true);

    heartbeat_initialize(PICO_DEFAULT_LED_PIN);

    i2c_init(i2c_default, 400000);
    gpio_set_function(PICO_DEFAULT_I2C_SDA_PIN, GPIO_FUNC_I2C);
    gpio_set_function(PICO_DEFAULT_I2C_SCL_PIN, GPIO_FUNC_I2C);

    gpio_init(MICRO_DEFAULT_SERVO_ENABLE);
    gpio_set_dir(MICRO_DEFAULT_SERVO_ENABLE, GPIO_OUT);
    gpio_put(MICRO_DEFAULT_SERVO_ENABLE, 0);

    sleep_ms(2500);

    info_cmd_func();
    stdio_flush();

    logger.initialize(true);
    logger.initialize_circular_buffer(PAD_BUFFER_SIZE);

    alt.initialize();
    sleep_ms(500);
    adxl375.initialize();
    sleep_ms(500);
    iim42653.initialize();
    sleep_ms(500);
    mmc5983ma.initialize();
    sleep_ms(500);
    pwm.init();

    kalman_verticality_init();

    xTaskCreate(heartbeat_task, "heartbeat", 256, NULL, HEARTBEAT_TASK_PRIORITY, NULL);
    xTaskCreate(serial_task, "serial", 8192, NULL, SERIAL_TASK_PRIORITY, NULL);

    xTaskCreate(MS5607::update_ms5607_task, "update_ms5607", 256, &alt, SENSOR_SAMPLE_PRIORITY, &(alt.update_task_handle));
    xTaskCreate(ADXL375::update_adxl375_task, "update_adxl375", 256, &adxl375, SENSOR_SAMPLE_PRIORITY, &(adxl375.update_task_handle));
    xTaskCreate(IIM42653::update_iim42653_task, "update_iim42653", 256, &iim42653, SENSOR_SAMPLE_PRIORITY, &(iim42653.update_task_handle));
    xTaskCreate(MMC5983MA::update_mmc5983ma_task, "update_mmc5983ma", 256, &mmc5983ma, SENSOR_SAMPLE_PRIORITY, &(mmc5983ma.update_task_handle));

    xTaskCreate(MS5607::ms5607_sample_handler, "ms5607_sample_handler", 256, &alt, SENSOR_EVENT_HANDLER_PRIORITY, &(alt.sample_handler_task_handle));

    xTaskCreate(rocket_task, "rocket_task", 512, NULL, SENSOR_SAMPLE_PRIORITY, const_cast<TaskHandle_t *>(&rocket_task_handle));
#if (DEBUG != 1)
    xTaskCreate(kalman_task, "kalman_task", 512, NULL, KALMAN_TASK_PRIORITY, const_cast<TaskHandle_t *>(&kalman_task_handle));
    vTaskCoreAffinitySet(kalman_task_handle, 0x01);
#endif
    vTaskCoreAffinitySet( alt.update_task_handle, 0x01 );
    vTaskCoreAffinitySet( adxl375.update_task_handle, 0x01 );
    vTaskCoreAffinitySet( iim42653.update_task_handle, 0x01 );
    vTaskCoreAffinitySet( mmc5983ma.update_task_handle, 0x01 );

    vTaskCoreAffinitySet(rocket_task_handle, 0x01);

    vTaskCoreAffinitySet( alt.sample_handler_task_handle, 0x01 );

    xTaskCreate(logging_task, "logging", 256, NULL, LOGGING_PRIORITY, const_cast<TaskHandle_t *>(&logging_handle));
    vTaskCoreAffinitySet(logging_handle, 0x02);

    vTaskStartScheduler();

    while (1) {
        tight_loop_contents();
    }
}

/****************************** LOGGING ***************************************/
static void populate_log_entry(log_entry_t* log_entry) {
    log_entry->time_us = time_us_64();

    adc_select_input(4);
    log_entry->temperature_chip = adc_read();
    log_entry->state = rocket_state;
    log_entry->deploy_percent = deployment_percent;
    log_entry->pressure = alt.get_pressure();
    log_entry->altitude = alt.get_altitude();
    log_entry->altitude_filt = altitude_filt;
    log_entry->velocity_filt = velocity_filt;
    log_entry->temperature_alt = alt.get_temperature();

    log_entry->ax = iim42653.get_ax();
    log_entry->ay = iim42653.get_ay();
    log_entry->az = iim42653.get_az();
    log_entry->gx = iim42653.get_gx();
    log_entry->gy = iim42653.get_gy();
    log_entry->gz = iim42653.get_gz();

    log_entry->mag_x = mmc5983ma.get_ax();
    log_entry->mag_y = mmc5983ma.get_ay();
    log_entry->mag_z = mmc5983ma.get_az();

    log_entry->high_g_x = adxl375.get_ax();
    log_entry->high_g_y = adxl375.get_ay();
    log_entry->high_g_z = adxl375.get_az();

    log_entry->drag_force = drag_force;
    log_entry->apogee_prediction = apogee_prediction;
    log_entry->desired_drag_force = desired_drag_force;

    log_entry->data0 = get_rand_32();
}

static void logging_task(void* pvParameters) {
    TickType_t xLastWakeTime;
    const TickType_t xFrequency = pdMS_TO_TICKS(1000 / LOG_RATE_HZ);

    xLastWakeTime = xTaskGetTickCount();
    while (1) {
        vTaskDelayUntil(&xLastWakeTime, xFrequency);
        populate_log_entry(const_cast<log_entry_t *>(&log_entry));
        if (serial_data_output) {
            print_log_entry(reinterpret_cast<const uint8_t *>(const_cast<log_entry_t *>(&log_entry)));
            stdio_flush();
        }

        if (use_circular_buffer) {
            logger.write_circular_buffer(reinterpret_cast<const uint8_t *>(const_cast<log_entry_t *>(&log_entry)));
            if (rocket_state != PAD) {
                logger.flush_circular_buffer(true);
                use_circular_buffer = false;
            }
        } else {
            logger.write_memory(reinterpret_cast<const uint8_t *>(const_cast<log_entry_t *>(&log_entry)), false);
        }
        if ((xLastWakeTime + xFrequency) < xTaskGetTickCount()) {
            xLastWakeTime = xTaskGetTickCount();
        }
    }
}
/****************************** LOGGING ***************************************/

/****************************** SERIAL CONSOLE ********************************/
static void read_cmd_func() {
    if (logging_handle != NULL) {
        vTaskSuspend(logging_handle);
    }
    logger.read_memory();
    if (logging_handle != NULL) {
        vTaskResume(logging_handle);
    }
}

static void write_cmd_func() {
    if (logging_handle != NULL) {
        vTaskSuspend(logging_handle);
    }
    uint64_t start = time_us_64();
    log_entry_t log_entry;
    populate_log_entry(&log_entry);
    printf("\nWriting the following entry!\n");
    print_log_entry(reinterpret_cast<const uint8_t *>(&log_entry));
    if (use_circular_buffer) {
        logger.write_circular_buffer(reinterpret_cast<const uint8_t *>(&log_entry));
    } else {
        logger.write_memory(reinterpret_cast<const uint8_t *>(&log_entry), true);
    }
    uint64_t end = time_us_64();
    printf("\nTook %" PRIu64 " us to write that entry!\n", (end - start));
    if (logging_handle != NULL) {
        vTaskResume(logging_handle);
    }
}

static void erase_cmd_func() {
    if (logging_handle != NULL) {
        vTaskSuspend(logging_handle);
    }
    logger.erase_memory();
    if (logging_handle != NULL) {
        vTaskResume(logging_handle);
    }
}

static void show_cmd_func() {
    serial_data_output = !serial_data_output;
}

static void deploy_cmd_func() {
    vTaskSuspend(rocket_task_handle);
    printf("Enabling servo!\n");
    gpio_put(MICRO_DEFAULT_SERVO_ENABLE, 1);
    vTaskDelay(pdMS_TO_TICKS(1000));
    printf("Setting servo to 80%\n");
    pwm.set_servo_percent(80);
    vTaskDelay(pdMS_TO_TICKS(5000));
    printf("Setting servo to 0%\n");
    pwm.set_servo_percent(0);
    vTaskDelay(pdMS_TO_TICKS(5000));
    printf("Setting servo to 80%\n");
    pwm.set_servo_percent(80);
    vTaskDelay(pdMS_TO_TICKS(5000));
    printf("Setting servo to 0%\n");
    pwm.set_servo_percent(0);
    vTaskDelay(pdMS_TO_TICKS(5000));
    printf("Disabling servo!\n");
    gpio_put(MICRO_DEFAULT_SERVO_ENABLE, 0);
    vTaskResume(rocket_task_handle);
}

#if (DEBUG == 1)
#include "ohio_test_data.h"
#endif

static void kalman_cmd_func() {
    static mf16* state_vector = kalman_get_state_vector(&kf);
    printf("Perfoming Kalman Filter Test! Stand back!\n");
    printf("*******************************************\n");
    printf("\naltitude,velocity,acceleration,drag_force,apogee_prediction,desired_drag_force,desired_deployment\n");

    fix16_t drag_force_l = 0;
    fix16_t apogee_prediction_l = 0;
    fix16_t desired_drag_force_l = 0;
    fix16_t desired_deployment_l = 0;
#if (DEBUG == 1)
    for (uint32_t i = 0; i < 7500; i++) {
        kalman_update(altitude_test_data[i], fix16_mul(fix16_sub(acceleration_data[i], fix16_one), F16(9.81f)));

        if (i >= 693 && i <= 1632) {
            drag_force_l = calculate_drag_force(fix16_from_int(80), state_vector->data[1][0]);
        } else {
            drag_force_l = calculate_drag_force(0, state_vector->data[1][0]);
        }
        apogee_prediction_l = predict_apogee(state_vector->data[0][0], state_vector->data[1][0], drag_force_l);
        desired_drag_force_l = calculate_desired_drag_force(state_vector->data[0][0], state_vector->data[1][0]);
        desired_deployment_l = calculate_deployment_percentage(desired_drag_force_l, state_vector->data[1][0]);
        desired_deployment_l = fix16_clamp(desired_deployment_l, 0, fix16_from_int(100));
        printf("%4.2f,%4.2f,%4.2f,%4.2f,%4.2f,%4.2f,%4.2f\n", fix16_to_float(state_vector->data[0][0]), fix16_to_float(state_vector->data[1][0]), fix16_to_float(fix16_mul(acceleration_data[i], F16(9.81f))), fix16_to_float(drag_force_l), fix16_to_float(apogee_prediction_l), fix16_to_float(desired_drag_force_l), fix16_to_float(desired_deployment_l));
        stdio_flush();
    }
#else
    kalman_update(0, 0);
#endif
}
/****************************** SERIAL CONSOLE ********************************/


static void rocket_task(void* pvParameters) {
    TickType_t xLastWakeTime;
    const TickType_t xFrequency = pdMS_TO_TICKS(1000 / ROCKET_TASK_RATE_HZ);

    vTaskDelay(pdMS_TO_TICKS(1000));
    ground_altitude = alt.get_altitude();

    // Sign of life
    gpio_put(MICRO_DEFAULT_SERVO_ENABLE, 1);
    pwm.set_servo_percent(0);
    vTaskDelay(pdMS_TO_TICKS(1000));
    pwm.set_servo_percent(20);
    vTaskDelay(pdMS_TO_TICKS(3000));
    pwm.set_servo_percent(0);
    vTaskDelay(pdMS_TO_TICKS(3000));
    pwm.set_servo_percent(20);
    vTaskDelay(pdMS_TO_TICKS(3000));
    pwm.set_servo_percent(0);
    vTaskDelay(pdMS_TO_TICKS(3000));
    gpio_put(MICRO_DEFAULT_SERVO_ENABLE, 0);

    xTaskCreate(launch_event_handler_task, "launch_event_handler", 512, NULL, ROCKET_EVENT_HANDLER_PRIORITY, const_cast<TaskHandle_t *>(&launch_event_handler_task_handle));
    vTaskCoreAffinitySet(launch_event_handler_task_handle, 0x01);
    alt.set_threshold_altitude(ground_altitude + (threshold_altitude * ALTITUDE_SCALE), &launch_event_callback);

    xLastWakeTime = xTaskGetTickCount();
    while (1) {
        vTaskDelayUntil(&xLastWakeTime, xFrequency);

        drag_force = calculate_drag_force(fix16_from_int(deployment_percent), velocity_filt);
        apogee_prediction = predict_apogee(altitude_filt, velocity_filt, drag_force);
        desired_drag_force = calculate_desired_drag_force(altitude_filt, velocity_filt);
        desired_deployment = calculate_deployment_percentage(desired_drag_force, velocity_filt);
        desired_deployment = fix16_clamp(desired_deployment, 0, fix16_from_int(100));
        uint8_t desired_deployment_uint8 = static_cast<uint8_t>(std::abs(desired_deployment >> 16));

        switch(rocket_state) {
            case PAD:
                deployment_percent = 0;
                pwm.set_servo_percent(deployment_percent);
                gpio_put(MICRO_DEFAULT_SERVO_ENABLE, 0);
                break;
            case BOOST:
                gpio_put(MICRO_DEFAULT_SERVO_ENABLE, 1);
                deployment_percent = 0;
                pwm.set_servo_percent(deployment_percent);
                break;
            case COAST:
                gpio_put(MICRO_DEFAULT_SERVO_ENABLE, 1);
                if (velocity_filt <= 0) {
                    rocket_state = APOGEE;
                    populate_log_entry(const_cast<log_entry_t *>(&log_entry));
                    logger.write_memory(reinterpret_cast<const uint8_t *>(const_cast<log_entry_t *>(&log_entry)), false);
                    deployment_percent = 0;
                    pwm.set_servo_percent(deployment_percent);
                    rocket_state = RECOVERY;
                    xTaskCreate(end_event_handler_task, "end_event_handler", 1024, NULL, ROCKET_EVENT_HANDLER_PRIORITY, const_cast<TaskHandle_t *>(&end_event_handler_task_handle));
                    vTaskCoreAffinitySet(end_event_handler_task_handle, 0x01);
                    add_alarm_in_ms(450000, end_event_callback, NULL, false);
                }
                deployment_percent = desired_deployment_uint8;
                if ((alt.get_altitude() - ground_altitude)> (2895 * ALTITUDE_SCALE)) {
                    deployment_percent = 100;
                }
                pwm.set_servo_percent(deployment_percent);
                break;
            case APOGEE:
                gpio_put(MICRO_DEFAULT_SERVO_ENABLE, 1);
                deployment_percent = 0;
                pwm.set_servo_percent(deployment_percent);
                break;
            case RECOVERY:
                gpio_put(MICRO_DEFAULT_SERVO_ENABLE, 1);
                deployment_percent = 0;
                pwm.set_servo_percent(deployment_percent);
                break;
            case END:
                deployment_percent = 0;
                pwm.set_servo_percent(deployment_percent);
                vTaskDelay(pdMS_TO_TICKS(1000));
                gpio_put(MICRO_DEFAULT_SERVO_ENABLE, 0);
                vTaskDelete(logging_handle);
                vTaskDelete(end_event_handler_task_handle);
                vTaskDelete(rocket_task_handle);
                break;
        }

        if ((xLastWakeTime + xFrequency) < xTaskGetTickCount()) {
            xLastWakeTime = xTaskGetTickCount();
        }
    }
}

static void kalman_task(void* pvParameters) {
    TickType_t xLastWakeTime;
    const TickType_t xFrequency = pdMS_TO_TICKS(1000 / KALMAN_TASK_RATE_HZ);

    const fix16_t accel_scale = fix16_div(F16(9.81f), F16(S_IIM42653_ACCEL_SENSITIVITY_FACTOR));

    mf16* state_vector = kalman_get_state_vector(&kf);
    fix16_t altitude_agl = 0;
    fix16_t vertical_accel = 1;

    xLastWakeTime = xTaskGetTickCount();
    while (1) {
        vTaskDelayUntil(&xLastWakeTime, xFrequency);
        taskENTER_CRITICAL();
        altitude_agl = fix16_div(fix16_from_int(alt.get_altitude() - ground_altitude), fix16_from_int(ALTITUDE_SCALE));
        vertical_accel = fix16_mul(fix16_sub(fix16_from_int(iim42653.get_az()), fix16_one), accel_scale);
        kalman_update(altitude_agl, vertical_accel);
        altitude_filt = state_vector->data[0][0];
        velocity_filt = state_vector->data[1][0];
        taskEXIT_CRITICAL();
        if ((xLastWakeTime + xFrequency) < xTaskGetTickCount()) {
            xLastWakeTime = xTaskGetTickCount();
        }
    }
}

static void launch_event_handler_task(void* pvParameters) {
    const TickType_t xInterruptFrequency = pdMS_TO_TICKS( 1000 );
    const TickType_t xMaxExpectedBlockTime = xInterruptFrequency + pdMS_TO_TICKS( 500 );
    uint32_t ulEventsToProcess;
    while (1) {
        /* Wait to receive a notification sent directly to this task from the
        interrupt service routine. */
        ulEventsToProcess = ulTaskNotifyTake( pdTRUE, xMaxExpectedBlockTime );
        if( ulEventsToProcess != 0 ) {
            /* To get here at least one event must have occurred. Loop here
            until all the pending events have been processed */
            while( ulEventsToProcess > 0 ) {
                vTaskSuspendAll();
                rocket_state = BOOST;
                xTaskCreate(coast_event_handler_task, "coast_event_handler", 512, NULL, ROCKET_EVENT_HANDLER_PRIORITY, const_cast<TaskHandle_t *>(&coast_event_handler_task_handle));
                vTaskCoreAffinitySet(coast_event_handler_task_handle, 0x01);
                add_alarm_in_ms(MOTOR_BURN_TIME, coast_event_callback, NULL, false);
                vTaskDelete(launch_event_handler_task_handle);
                launch_event_handler_task_handle = NULL;
                xTaskResumeAll();
            }
        }
    }
}

static void coast_event_handler_task(void* pvParameters) {
    const TickType_t xInterruptFrequency = pdMS_TO_TICKS( MOTOR_BURN_TIME );
    const TickType_t xMaxExpectedBlockTime = xInterruptFrequency + pdMS_TO_TICKS( 500 );
    uint32_t ulEventsToProcess;
    while (1) {
        /* Wait to receive a notification sent directly to this task from the
        interrupt service routine. */
        ulEventsToProcess = ulTaskNotifyTake( pdTRUE, xMaxExpectedBlockTime );
        if( ulEventsToProcess != 0 ) {
            /* To get here at least one event must have occurred. Loop here
            until all the pending events have been processed */
            while( ulEventsToProcess > 0 ) {
                vTaskSuspendAll();
                rocket_state = COAST;
                vTaskDelete(coast_event_handler_task_handle);
                coast_event_handler_task_handle = NULL;
                xTaskResumeAll();
            }
        }
    }
}
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

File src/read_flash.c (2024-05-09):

#include <stdio.h>
#include <inttypes.h>
#include "boards/pico_w.h"
#include "hardware/spi.h"
#include "spi_flash.h"

int main() {
    stdio_init_all();
    getchar();
    // Enable SPI 0 at 1 MHz and connect to GPIOs
    spi_init(spi_default, 1000 * 1000 * 60);
    gpio_set_function(PICO_DEFAULT_SPI_RX_PIN, GPIO_FUNC_SPI);
    gpio_set_function(PICO_DEFAULT_SPI_TX_PIN, GPIO_FUNC_SPI);
    gpio_set_function(PICO_DEFAULT_SPI_SCK_PIN, GPIO_FUNC_SPI);

    // Chip select is active-low, so we'll initialise it to a driven-high state
    gpio_init(PICO_DEFAULT_SPI_CSN_PIN);
    gpio_set_dir(PICO_DEFAULT_SPI_CSN_PIN, GPIO_OUT);
    gpio_put(PICO_DEFAULT_SPI_CSN_PIN, 1);

    uint8_t entry[PACKET_SIZE];

    // flash_erase(spi_default, PICO_DEFAULT_SPI_CSN_PIN);
    flash_read(spi_default, PICO_DEFAULT_SPI_CSN_PIN, base_addr, page_buffer, FLASH_PAGE_SIZE);
    for (uint16_t i = 0; i < FLASH_PAGE_SIZE; i += PACKET_SIZE) {
        if (page_buffer[i] == 0xFF) {
            base_addr += i;
            break;
        }
        if ((i + PACKET_SIZE) == FLASH_PAGE_SIZE) {
            base_addr += FLASH_PAGE_SIZE;
            flash_read(spi_default, PICO_DEFAULT_SPI_CSN_PIN, base_addr, page_buffer, FLASH_PAGE_SIZE);
            i = 0;
        }
    }

    printf("\nRead Data:\n");
    printf("time (us) | state | dep pcnt | alt (m) | vel (m/s) | quat_w | quat_x | quat_y | quat_z | lin_ax | lin_ay | lin_az\n");
    for (uint32_t i = 0; i < base_addr; i += PACKET_SIZE) {
        flash_read(spi_default, PICO_DEFAULT_SPI_CSN_PIN, i, entry, PACKET_SIZE);
        uint64_t now_us = (((uint64_t)entry[0] << 56) | ((uint64_t)entry[1] << 48) | \
                          ((uint64_t)entry[2] << 40)  | ((uint64_t)entry[3] << 32) | \
                          ((uint64_t)entry[4] << 24)  | ((uint64_t)entry[5] << 16) | \
                          ((uint64_t)entry[6] << 8)   | ((uint64_t)entry[7]));

        uint8_t state = entry[8];
        uint8_t deploy_percent = entry[9];

        uint32_t alt_bits = (entry[10] << 24) | (entry[11] << 16) | (entry[12] << 8) | (entry[13]);
        uint32_t vel_bits = (entry[14] << 24) | (entry[15] << 16) | (entry[16] << 8) | (entry[17]);
        float altitude = *(float *)(&alt_bits);
        float velocity = *(float *)(&vel_bits);

        int16_t w = ((int16_t)entry[18]) | (((int16_t)entry[19]) << 8);
        int16_t x = ((int16_t)entry[20]) | (((int16_t)entry[21]) << 8);
        int16_t y = ((int16_t)entry[22]) | (((int16_t)entry[23]) << 8);
        int16_t z = ((int16_t)entry[24]) | (((int16_t)entry[25]) << 8);
        float qw = ((float)w) / 16384.0; // 2^14 LSB
        float qx = ((float)x) / 16384.0;
        float qy = ((float)y) / 16384.0;
        float qz = ((float)z) / 16384.0;
        int16_t ax = ((int16_t)entry[26]) | (((int16_t)entry[27]) << 8);
        int16_t ay = ((int16_t)entry[28]) | (((int16_t)entry[29]) << 8);
        int16_t az = ((int16_t)entry[30]) | (((int16_t)entry[31]) << 8);
        float lax = ((float)x) / 100.0;
        float lay = ((float)y) / 100.0;
        float laz = ((float)z) / 100.0;
        printf("%"PRIu64" | %c | %"PRIu8" | %4.2f | %4.2f | %4.2f | %4.2f| %4.2f | %4.2f | %4.2f | %4.2f |%4.2f\n", \
                now_us, state, deploy_percent, altitude, velocity, qw, qx, qy, qz, lax, lay, laz);
    }
}

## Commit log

2023-11-12 Header styles and file naming conventions; CMake ARM Linux musl Compiler
2024-05-09 02/24/2024 Test Launch Version (BB Black) (#11)
    * Adding a 90% completed, compilable but untested ADS
    * Made basic changes to actuator & sensor. Also added motor class
    * Removed unnecessary .cpp files
    * Updated sensor & actuator classes, finished ads, added variable time step to kalman filter, set up all tests for future assertions
    * Relocated 'main' to 'active-drag-system.cpp'. Added more info to README
    * Removed main.cpp
    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
2024-05-09 Raspberry Pi Pico (#12)
    * Added more details to README
    * Changed some function parameters from pass-by-pointer to pass-by-reference. Also removed the std namespace
    * Started writing the test cases
    * Updated the .gitignore file
    * Removed some files that should be gitignored
    * Up to date w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
2024-06-13 Where to begin…. (#13)
    +/- Reworked collection of altimeter related functions into altimeter class
    +/- Reworked bno055 class to be imu class with minimal functionality
    \- Removed external Kalman filter implementations in favor of own in house version
    \- Removed any/unused files
    \+ Added buffer logger for when sitting on pad for extended period of time in effort to prevent filling of flash chip
    \+ Added heartbeat LED for alive status
    [active_drag_system.cpp, alt_test.cpp, read_flash.c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]
2025-01-30 RP2040 PCB: Rev 1
    [10118193-0001LF.step, ABM8AIG-12.000MHZ-12-2Z-T3.step, IIM-42653.step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]
2025-03-19 Rev 2 of Custom PCB but without Motor Driver (Replaced with Optocoupler Circuit for Standard Servo) (#15)
    [STP55NF06.step, active-drag-system.kicad_pcb, active-drag-system.kicad_sch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]
2025-06-20 Big Kahuna - IREC 2025 - Dawsyn's Final Commit (#16)
    # Dawsyn's Final Commit
    This one is a little emotional as this is my final commit in this repository and as a member of Rocketry at Virginia Tech. This merges the changes seen in the branch known as 'big_kahuna' into main. This is the version of the ADS software as seen on [Roadkill](https://drive.google.com/file/d/120BvI-0ntliHo6i9UxcCn2pXAl-JsdP_/view?usp=drive_link) in the 2025 IREC competition. There are bound to be bugs, but I have found it useful to have the final competition version to be the one present on main at the end of every academic year. Hopefully this is useful to the next lead.
    ## Primary Changes
    + NEW I2C drivers to su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
    [active_drag_system.cpp, adxl375.cpp, alt_test.cpp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]
2025-10-08 Fixed headers in log_format.hpp and active_drag_system.cpp to allow for WSL CMake compilation
    [active_drag_system.cpp]
2026-02-01 Updated CMakes to build correctly
    [read_flash.cpp]
2026-03-22 Copied in Jhamar's kalman filter port for further development
2026-06-07 Fixed the clamping issue
    [active_drag_system.cpp]
2026-06-07 Modified the clamp fix to remove division
    [active_drag_system.cpp]

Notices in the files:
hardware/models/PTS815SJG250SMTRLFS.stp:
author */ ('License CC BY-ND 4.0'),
